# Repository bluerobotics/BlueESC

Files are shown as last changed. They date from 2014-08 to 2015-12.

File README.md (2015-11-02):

BlueESC
=======

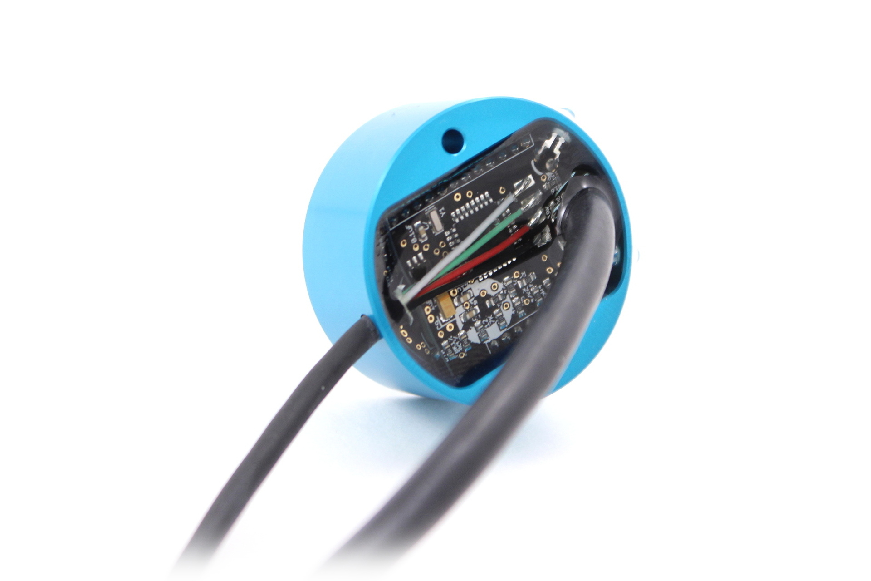
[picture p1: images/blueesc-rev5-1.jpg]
BlueESC Rev1 Prototype BlueESC Production Version


The BlueESC is a simple, open-source electronic speed controller for three-phase brushless motors. It is designed to run the [SimonK firmware](http://github.com/sim-/tgy) on an Atmega8 microcontroller.

The hardware is licensed under GPLv3. It was inspired by and draws from other open-source ESC projects including [AfroESC](https://code.google.com/p/afrodevices/), [WiiESC](https://code.google.com/p/wii-esc/), and others. We owe a big thanks to everyone who has shared their open-source ESC designs and firmware.

We also thank Bernhard Konze and SimonK for the [tgy firmware](http://github.com/sim-/tgy). Please see the firmware license at the top of [tgy.asm](https://github.com/bluerobotics/tgy/blob/master/tgy.asm). The firmware configuration files for the BlueESC are maintained in [our fork of the tgy project](http://github.com/bluerobotics/tgy).

##Features

* Atmega8 microcontroller
* PWM and I2C signal interfaces
* 5-22 volt input (2-5s lipo)
* Reprogrammable via PWM pin using bootloader (usblinker)
* Status and warning LED indicators
* Sensors for voltage, current, temperature, and RPM
* No battery-eliminator-circuit (BEC)
* N-Channel MOSFETs

##Current Generation: Rev. 5-8

The current major revision is designed to work with the [BlueRobotics T100 Thruster](http://www.bluerobotics.com/thruster/). It is highly compact and is potted in an aluminum enclosure that acts as a heat sink. The board is built with two 2-layer boards, one for the power electronics and one for logic. The boards are connected by headers. This allows components to be placed on three sides, simplifies design, and minimizes cost.

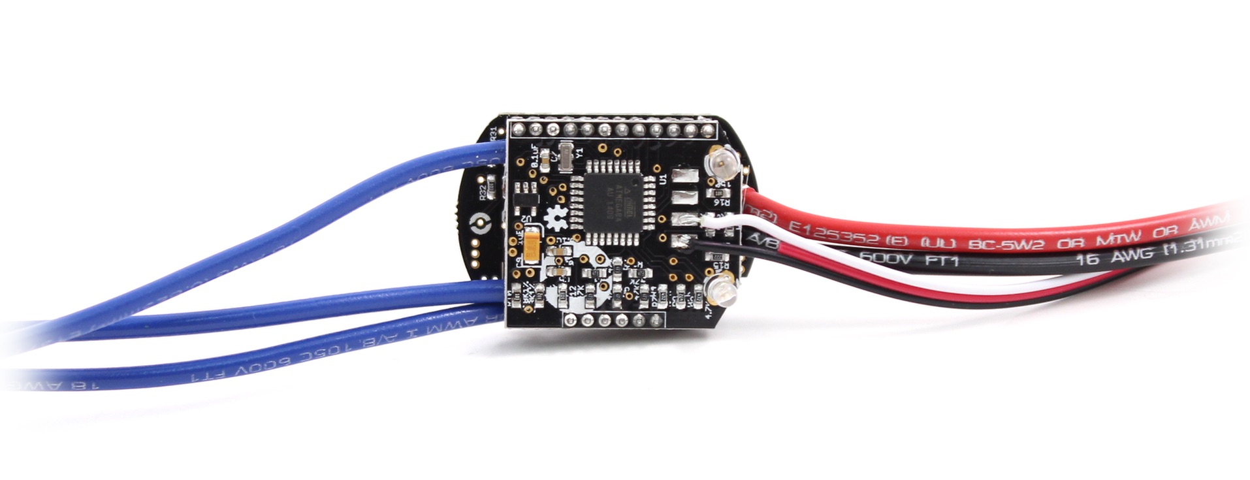
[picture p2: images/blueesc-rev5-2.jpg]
BlueESC Rev5 Board BlueESC Rev5 Without Enclosure


###Features

* Hall effect current sense IC (ACS711EX)
* Thermistor temperature sensor (10K)

###Specifications

* 6-22 volt input
* 25 amps continuous current (air)
* 35+ amps continuous current (water)
* 400 uF decoupling capacitance
* Enclosure diameter: 40 mm (1.58")
* Enclosure length: 18.5 mm (0.73")

###Design Files

**Schematic:** [BlueESC.pdf](https://github.com/bluerobotics/BlueESC/raw/master/BlueESC/BlueESC.pdf)

See repository for up-to-date EagleCAD schematic and board layout.

##Firmware Compilation

The BlueESC uses the [tgy firmware located in the BlueRobotics fork](https://github.com/bluerobotics/tgy).

*Mac:* (Uses Homebrew)

```bash
brew update
brew install avra
make blueesc.hex
```

##Initial Firmware Flashing

The BlueESC can be flashed using any AVR ISP programmer.

```bash
avrdude -c [programmer] -p m8 -U flash:w:blueesc.hex:i 
```

The fuses should be set per the instructions in the [tgy](http://github.com/sim-/tgy) instructions.

```bash
avrdude -c [programmer] -p m8 -U lfuse:w:0x3f:m -U hfuse:w:0xca:m
```

The Rev5 version of the board does not include an ISP header or pads. The microcontroller must be flashed with a special tool that connects directly to the microcontroller pins. Make sure that the board is powered when programming.

##Firmware Flashing Through Bootloader

Once the ESC has had the firmware (including bootloader) flashed the first time, it can be reprogrammed subsequently through the PWM input pin using a programmer like the [Turnigy USB Linker](http://www.hobbyking.com/hobbyking/store/__10628__turnigy_usb_linker_for_aquastar_super_brain.html). This can be done through the Makefile in the **tgy** project as follows.

```bash
make program_tgy_blueesc
```

It can also be done with avrdude and the compiled hex files as follows.

```bash
avrdude -c stk500v2 -b 19200 -P [programmer port] -p m8 -U flash:w:blueesc.hex:i
```

##I2C Commands and Address

*Please also see our [Arduino library for I2C ESC control](https://github.com/bluerobotics/Arduino_I2C_ESC).*

The I2C message format allows speed and direction to be set and voltage, current, rpm, temperature, and status to be requested.

###Speed Command (Register 0x00-0x01)
* cmd: Command, sent as int16_t. Full range, negative for reverse, positive for forward.
  * Forward: 0 to 32767
  * Reverse: 0 to -32767

####Bytes
* Byte 0: throttle_h
* Byte 1: throttle_l

###Sensor Data (Register 0x02-0x0A)
* pulse_count: Commutation pulses since last request. Sent as uint16_t.
  * Calculate rpm with pulse_count/dt*60/motor_pole_count
* voltage: ADC measurement scaled to 16 bits
  * Calculate voltage with voltage/2016
* temperature: ADC measurement scaled to 16 bits
  * Calculate temperature with the Steinhart equation
* current: ADC measurement scaled to 16 bits
  * Calculate current with (current-32767)/891

####Bytes
* Byte 0: pulse_count_h
* Byte 1: pulse_count_l
* Byte 2: voltage_h
* Byte 3: voltage_l
* Byte 4: temperature_h
* Byte 5: temperature_l
* Byte 6: current_h
* Byte 7: current_l
* Byte 8: 0xab (identifier to check if ESC is alive)

##Releases

v1.0 - Rev5. Currently shipping.

v1.1 - Rev6. Added PWM pull-down resistor and low pass filter for current sense. Switched to SMT LEDs. No changes to Power Board.

##Video

I2C Demonstration:

I2C Demonstration of BlueESC (https://www.youtube.com/watch?v=3BH41H-kpA8)

Testing of Final Prototype:

Final Prototype of BlueESC (https://www.youtube.com/watch?v=g5yOUzKvsxc)

Testing of First Prototype:

First Test of BlueESC (http://www.youtube.com/watch?feature=player_embedded&v=qJa0dBeoZHA)

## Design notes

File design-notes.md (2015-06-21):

##Design Notes for BlueESC

These design notes are written for the rev3 (two board) design, although they should pertain to the previous revisions as well.

##Component Selection

###MOSFETs

* Choose SiR158DP
* Max current is 30A and max duty cycle is about 33% (because it is three phase); Rdson is 0.0023 worst case and there are two FETs per phase so that P = 30^2*.33*.0023*2 = 1.36 W; This results in a junction-to-ambient rise of 23*1.36 = 31.3 C
* Output capacitance is 915 pF and input resistor is 100 ohm. Therefore, the RC time constant is 91.5 ns.
* According to (http://www.ti.com/lit/an/slva504/slva504.pdf), the switching power dissipation can be estimated as Psw = 0.5*(24V)*(30A)*(91.5E-9s)*(18000hz) = 0.60 W x 2 FETs = 1.20 W. This would lead to a temperature rise of 27.6 C.
* Using these numbers combined, the maximum temperature if ambient temp is 25C would be 84C. The max allowable temperature of the MOSFET is 150C.

#Other Collected Notes

MOSFETs:

Heat losses come from Rdson, which is usually small for most FETs. Rdson accounts for some of the heat.

More heat comes from the internal diodes, which are built into the silicon and are not Schottky. The reverse current spikes caused by the inductance of the motor causing back flowing current. The voltage drop turns into heat. This is most significant around the 50% duty cycle area. It's related to the switching frequency and the inductance of the motor.

If there is a lot of heat from diodes, external Schottky diodes could be added to reduce heat loss from voltage drop.

Choosing MOSFET and reading data sheet: The most important values for estimating performance are the temperature rise from junction to ambient per watt and the allowable temp, which should be derated. (Derates everything by x/0.6).

Most of the heat will be coming out of the big pad on the MOSFET, not the case. The copper there should be thick and large to distribute heat as well as possible. Hopefully the thermally conductive potting compound will help conduct heat from the traces.

The 100 ohm resistors that turn on the FETs are important to size properly, too large will turn them on slowly, increasing switching losses, and too small could cause the low side FETs to turn on accidentally. Recommended 22 ohm but  100 ohm was fine.

The charge pumps work by charging the capacitor to 12V when the low side is on, then when the high side turns on, the capacitor is already at 12V but the low side of the capacitor goes up to 12V, meaning that the high side of the capacitor is now 24V. It's only needed on the high side because the EMF of the motor is high when switching. Might be 10Vand Vin to MOSFET at 12V --> bad switching.

The charge pump diode needs to be sized the handle the current that rushes through it when switching. A small current limiting resistor could be used to help. 0.5-1.0 amp (what I have now) is more than sufficient.

The charge pump capacitor will never have more than the input voltage across it, so 12V or the max voltage.

If there are heat problems, it is most likely switching losses, then diode losses, then everything else.

CAPACITORS:

Recommend 500-1000uF for decoupling. Tantalums can be used, they have packages that are double high.

OTHER:

Strongly recommends current sensors to automatically limit current spikes when starting.

The software probably has a time delay between switching high and low, but you can also do it with hardware with a diode and sizing the resistors properly.

Guessed that motor inductance was 200-400 uH and that would be a low value for fast switching.

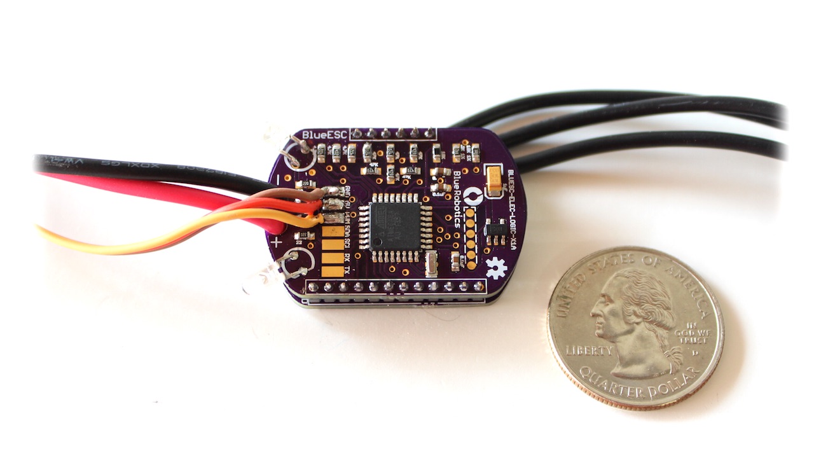
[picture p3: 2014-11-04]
images/blueesc-rev3-1.jpg

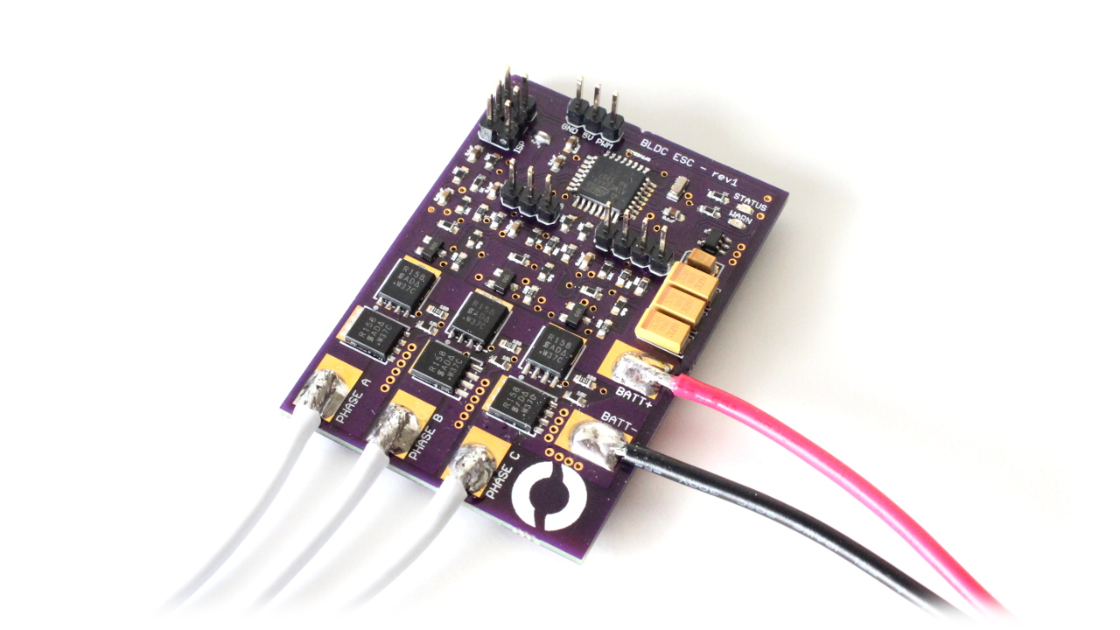
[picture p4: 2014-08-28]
images/blueesc-rev1-2.jpg

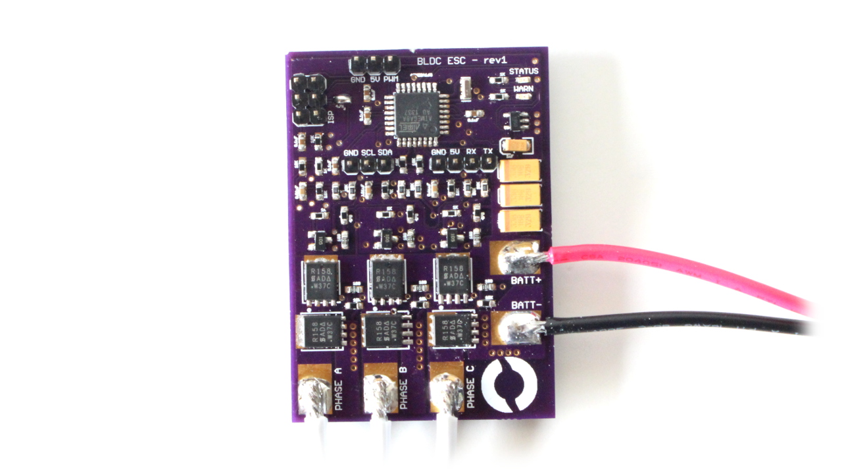
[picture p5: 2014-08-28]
images/blueesc-rev1-1.jpg

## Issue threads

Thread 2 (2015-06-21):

Low pass current sensor

rjehangir, 2015-06-21:
The current sensor bandwidth is too high causing slow measurements to require a large software low-pass filter for accuracy. A hardware low pass should be added to resolve this.

rjehangir, 2015-10-18:
A low pass filter has been added an makes a significant improvement to the current reading.

Closed 2015-10-18.

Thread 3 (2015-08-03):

PWM signal pull down

rjehangir, 2015-08-03:
Add a weak pull down to the PWM line so that it doesn't have to be grounded for I2C to work properly.

rjehangir, 2015-10-18:
A 470K resistor has been added and tested for correction function.

Closed 2015-10-18.

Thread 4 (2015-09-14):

BlueESC Control Logic I2C

gaitskell, 2015-09-14:
The manual doesn't explain what the red and blue LED's indicate on the integrated BlueESC. Also what does it mean when it beeps every few seconds?

I am able to read I2C data from the BlueESC but am unable to get prop spinning when writing I2C. Do you have any debug suggestions? Do you have to use PWM stop signal to activate motor, prior to being able to use I2C? I assume not? Do you have some I2C Python SBUS examples you could post to make sure I'm using your desired conventions? Thanks
Rickg@gaitskell.com

gaitskell, 2015-09-14:
Ok - so we figured it out by trial and error. I2C requires a write THROTTLE 0 for safety before a write THROTTLE 50 (finite speed). And you have to write <= 0.5 secs to avoid safety shutdown (which is a good feature). We filmed a video of the basic logic of operation and will post it on YouTube. Obviously, it would be great to get the online docs to include these aspects of I2C operation.

Closed 2015-09-14.

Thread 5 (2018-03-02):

Wrong RC time for the turn on of the upper FET in file "design-notes.md"

AGenchev, 2018-03-02:
Hello. I was looking for an ingenious design which would me allow to ditch the gate drivers I use, hence looked at the schematic in  https://github.com/bluerobotics/BlueESC/raw/master/BlueESC/BlueESC.pdf
But quickly realized that it will not perform on a par with the gate drivers (at least for the high side NMOSFETs).
The upper FETs are N-channel. They turn on with <b>positive</b> voltage on the gate relative to the source.
Watching the schematic in the https://github.com/bluerobotics/BlueESC/raw/master/BlueESC/BlueESC.pdf you can see that the upper FETs can get positive voltage on their gates from the high side of the capacitors via 100 Ω <b>plus 2.2 kΩ</b> resistors when the NPN transistors are OFF. This mean that the total resistance on this path is 2.3 kΩ, so the turn on RC constant is 10-20 times longer. E.t. instead of 100 nS, it goes at least to 1000 nS. This should lead to more heat generated by the upper FETs (if the charging pumps work as intended and supply higher than Vcc voltage to turn on the upper FETs).  You should use either more sophisticated push-pull high side gate driver or use an IC gate driver (which of course will make the BOM with higher cost).

Williangalvani, 2019-04-01:
As this repository is being archived and will see no further development, all issues are being closed.

Closed 2019-04-01.

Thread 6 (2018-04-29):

modular ESC

mkeyno, 2018-04-29:
Hi, sorry to open ticket for my question , actually I intend to made modular ESC in way that controller + gate driver is separated from Mosfets pcb , hence I could increase module ampere by adding parallel Mosfet in the Mosfets pcb, I really appreciated to have your advise or if you know open HW/SW sources let me know

Williangalvani, 2019-04-01:
As this repository is being archived and will see no further development, all issues are being closed.

Closed 2019-04-01.

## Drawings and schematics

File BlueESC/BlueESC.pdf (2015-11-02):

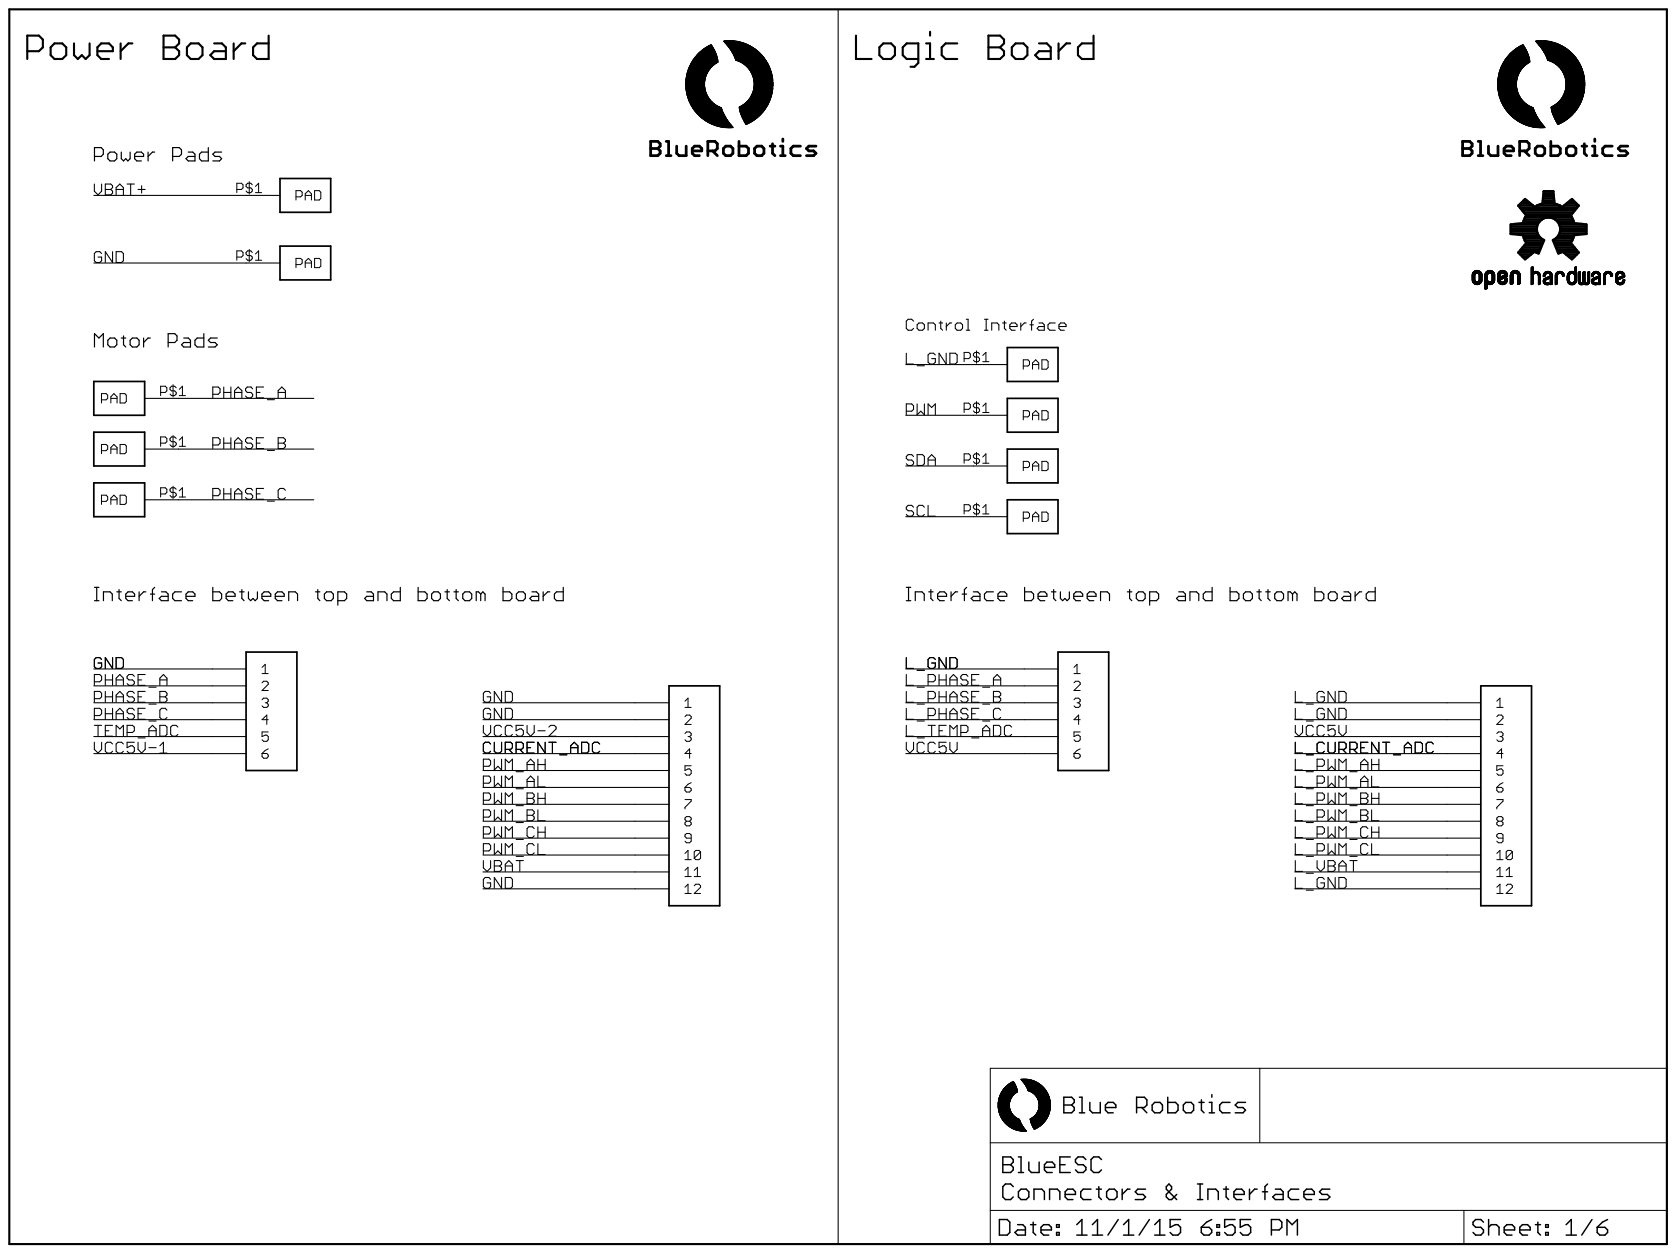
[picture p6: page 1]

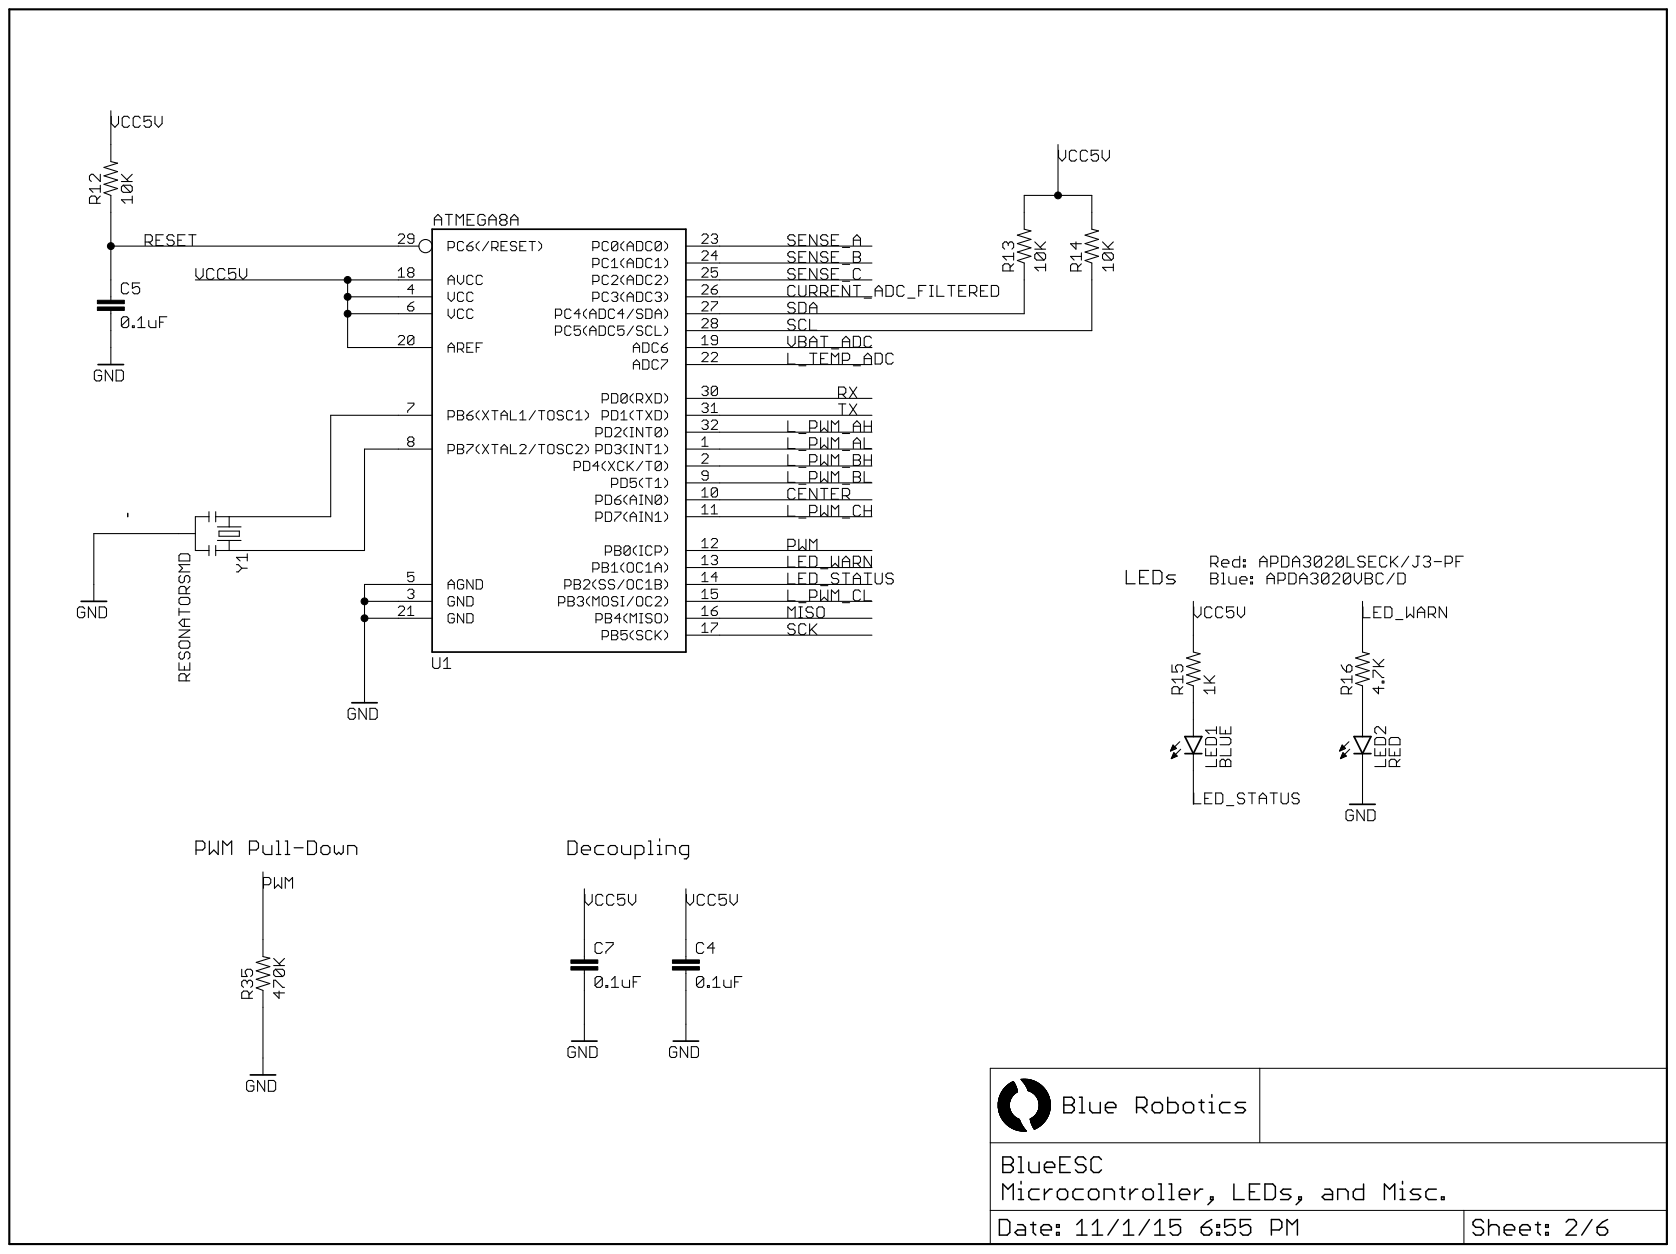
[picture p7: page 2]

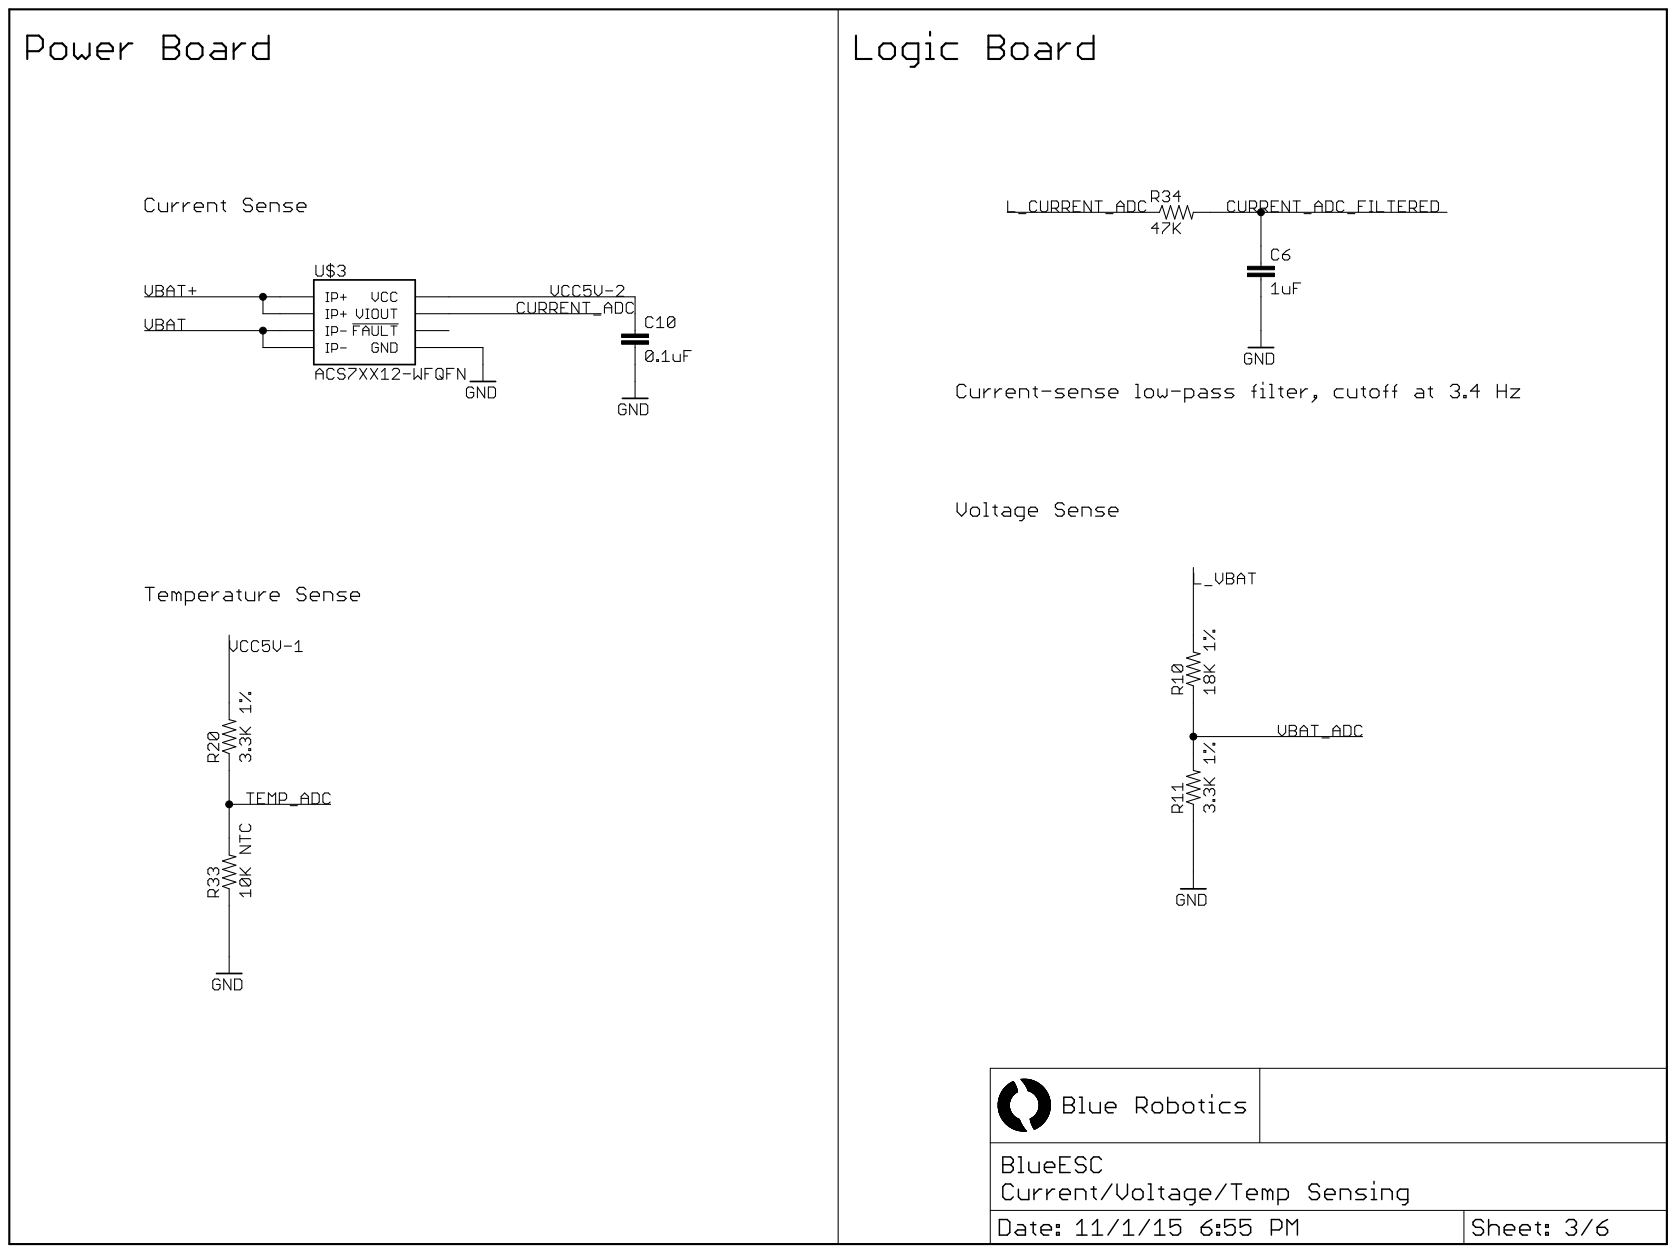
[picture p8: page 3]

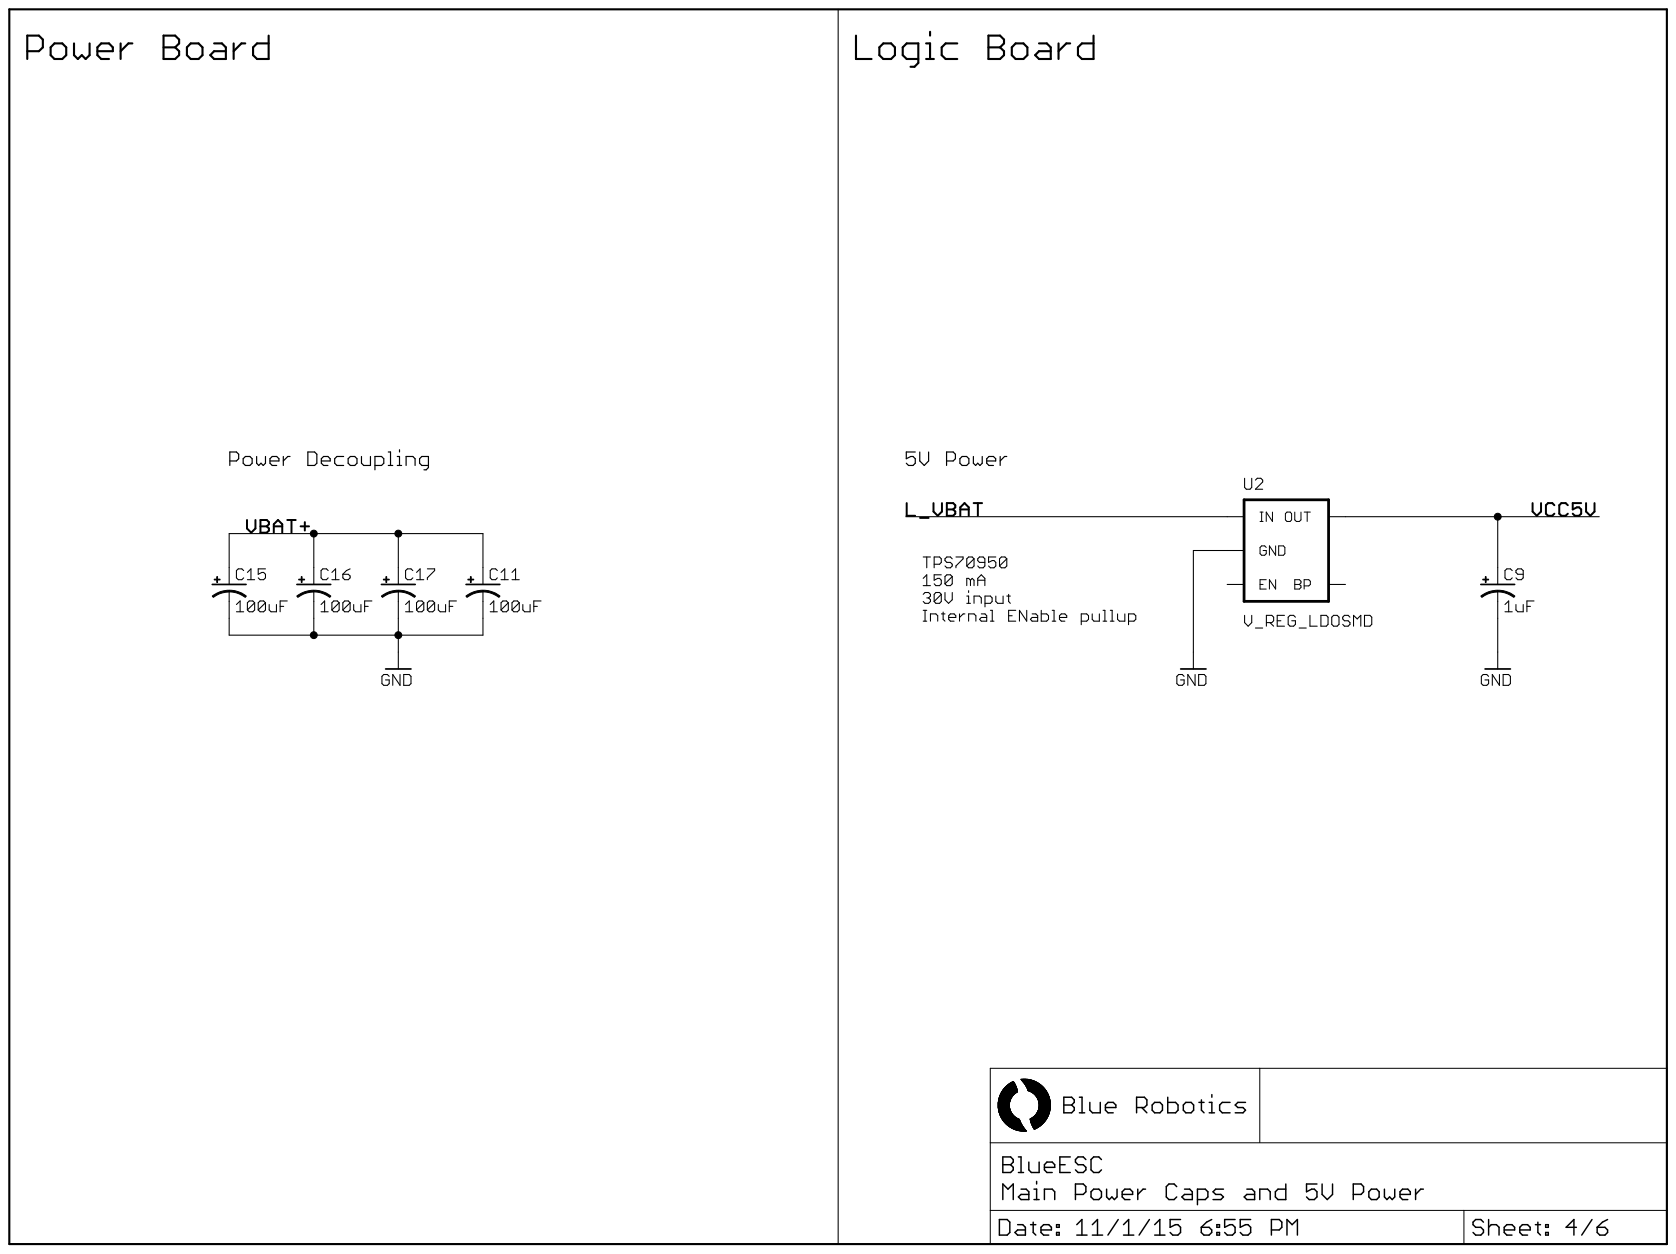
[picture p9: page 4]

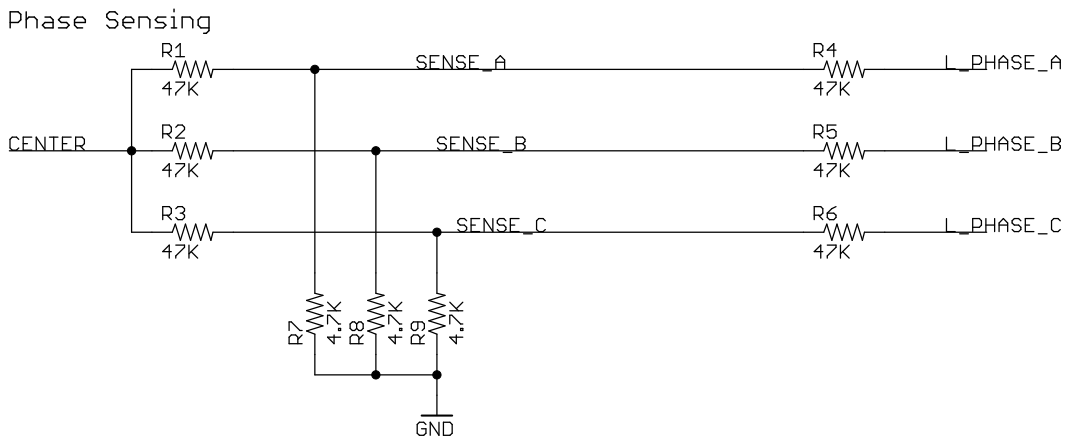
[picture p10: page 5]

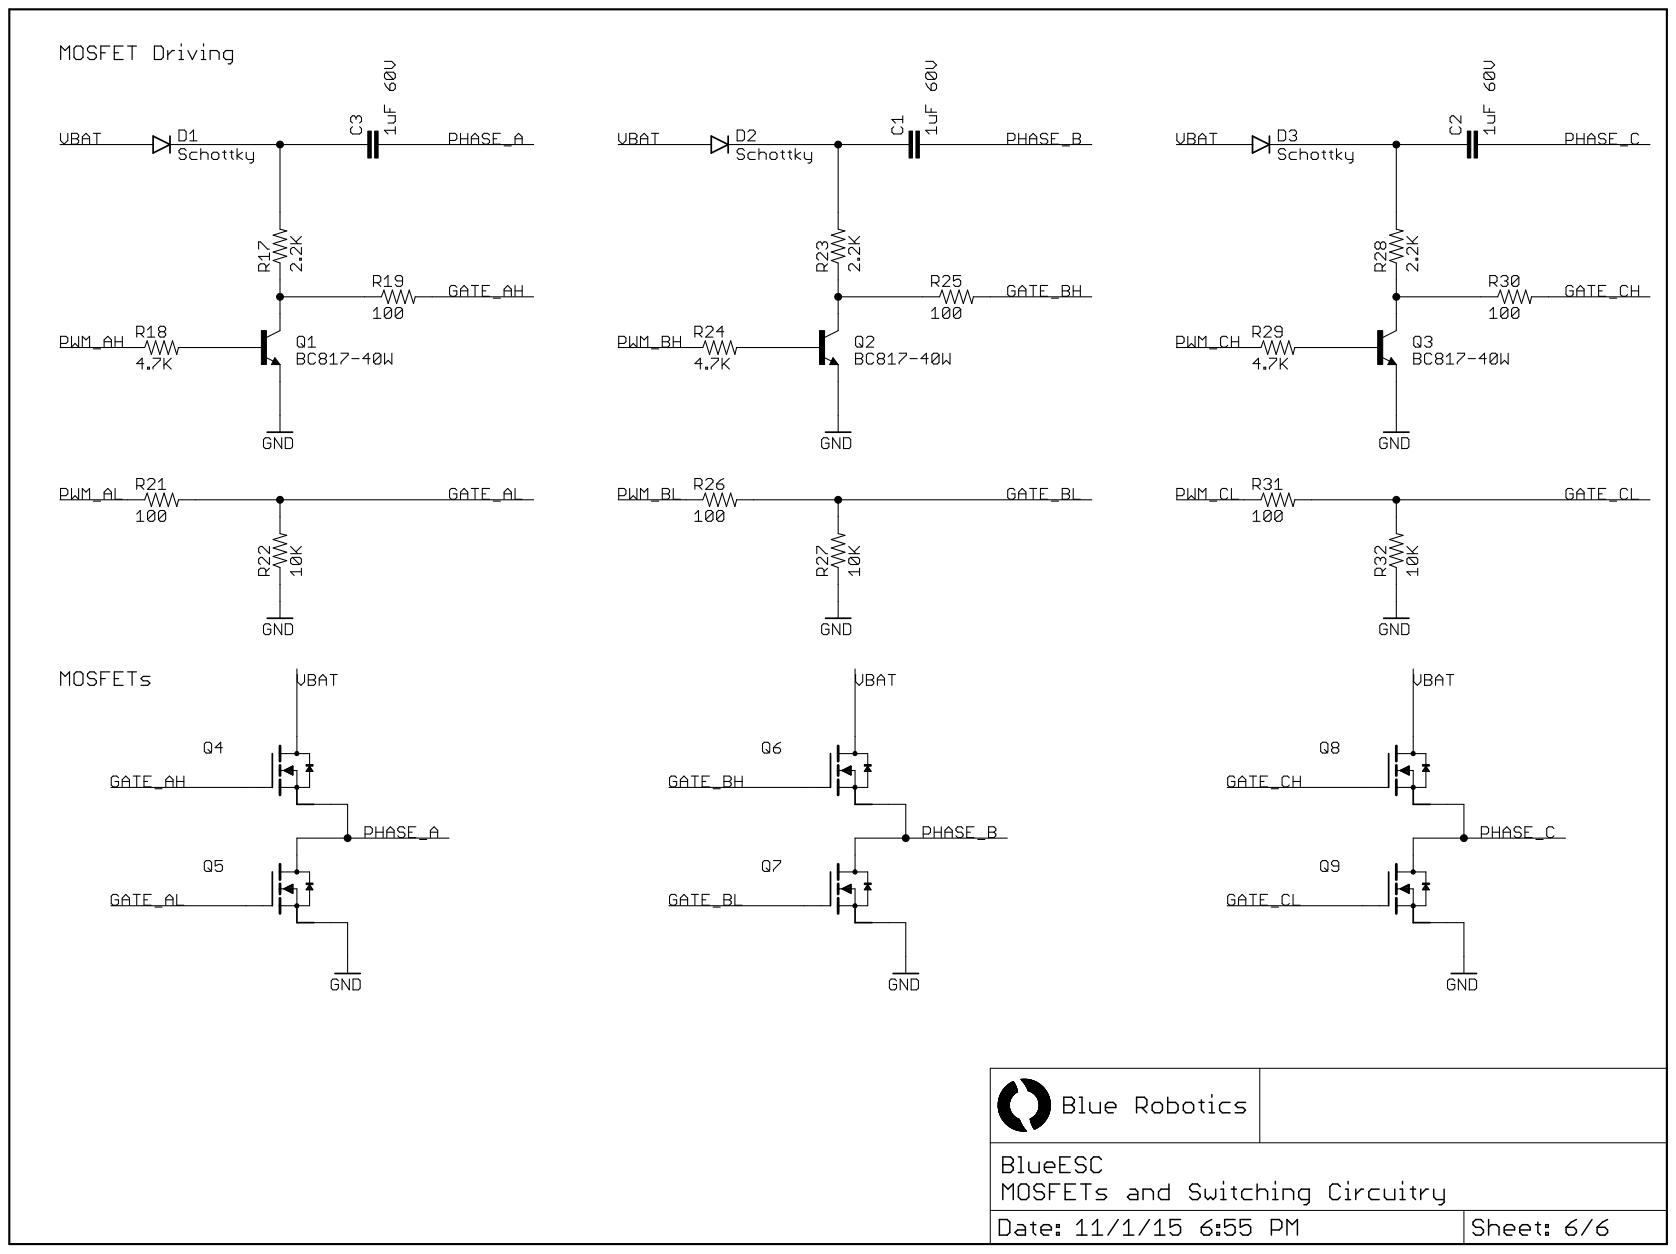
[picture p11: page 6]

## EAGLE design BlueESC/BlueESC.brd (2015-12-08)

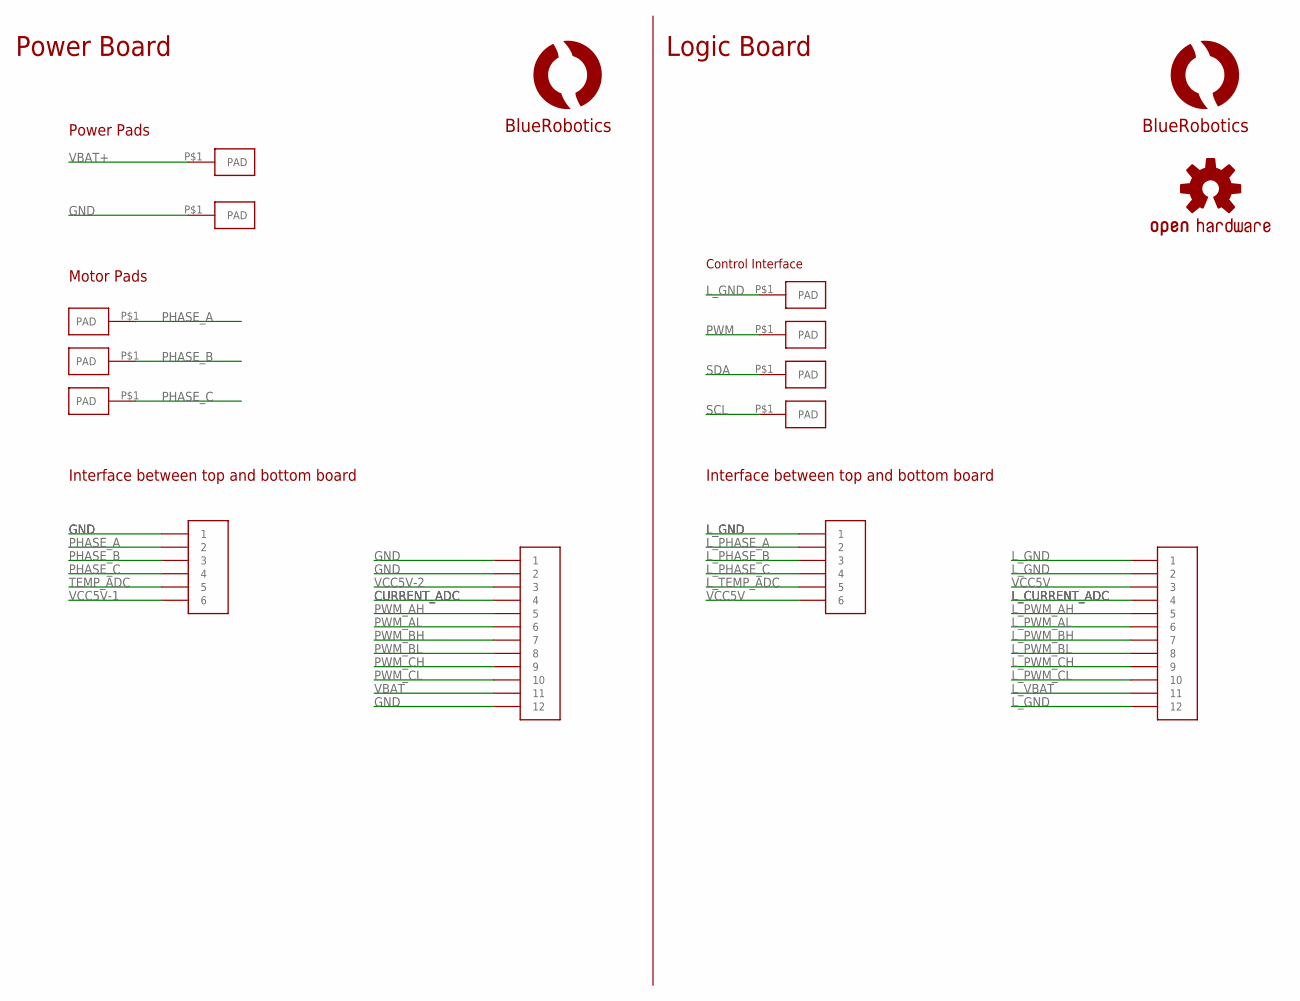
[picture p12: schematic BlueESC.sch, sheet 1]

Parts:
LOGO1: OSHW-LOGOS; OSHW-LOGO-S
U$1, U$2: PADPTH-MED; PAD-PTH-MED-1
U$4, U$16: HEADER-62MM; HEADER-2MM-6POS
U$5, U$6, U$7: PAD18AWG; PAD-PTH-18AWG-1
U$8, U$17: HEADER-122MM; HEADER-2MM-12POS
U$9: LOGOBR-LOGO-S; BR-LOGO-SMALL
U$10: LOGOBR-LOGO-M; BR-LOGO-MEDIUM
U$11, U$12, U$13, U$14: PAD1.5X3MM; PAD-1.5X3MM

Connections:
CURRENT_ADC: U$8.P$4 (4); also elsewhere on the board
GND: U$2.P$1, U$4.P$1 (1), U$8.P$1 (1), U$8.P$2 (2), U$8.P$12 (12); also elsewhere on the board
L_CURRENT_ADC: U$17.P$4 (4); also elsewhere on the board
L_GND: U$11.P$1, U$16.P$1 (1), U$17.P$1 (1), U$17.P$2 (2), U$17.P$12 (12); also elsewhere on the board
L_PHASE_A: U$16.P$2 (2); also elsewhere on the board
L_PHASE_B: U$16.P$3 (3); also elsewhere on the board
L_PHASE_C: U$16.P$4 (4); also elsewhere on the board
L_PWM_AH: U$17.P$5 (5); also elsewhere on the board
L_PWM_AL: U$17.P$6 (6); also elsewhere on the board
L_PWM_BH: U$17.P$7 (7); also elsewhere on the board
L_PWM_BL: U$17.P$8 (8); also elsewhere on the board
L_PWM_CH: U$17.P$9 (9); also elsewhere on the board
L_PWM_CL: U$17.P$10 (10); also elsewhere on the board
L_TEMP_ADC: U$16.P$5 (5); also elsewhere on the board
L_VBAT: U$17.P$11 (11); also elsewhere on the board
PHASE_A: U$4.P$2 (2), U$5.P$1; also elsewhere on the board
PHASE_B: U$4.P$3 (3), U$6.P$1; also elsewhere on the board
PHASE_C: U$4.P$4 (4), U$7.P$1; also elsewhere on the board
PWM: U$14.P$1; also elsewhere on the board
PWM_AH: U$8.P$5 (5); also elsewhere on the board
PWM_AL: U$8.P$6 (6); also elsewhere on the board
PWM_BH: U$8.P$7 (7); also elsewhere on the board
PWM_BL: U$8.P$8 (8); also elsewhere on the board
PWM_CH: U$8.P$9 (9); also elsewhere on the board
PWM_CL: U$8.P$10 (10); also elsewhere on the board
SCL: U$13.P$1; also elsewhere on the board
SDA: U$12.P$1; also elsewhere on the board
TEMP_ADC: U$4.P$5 (5); also elsewhere on the board
VBAT: U$8.P$11 (11); also elsewhere on the board
VBAT+: U$1.P$1; also elsewhere on the board
VCC5V: U$16.P$6 (6), U$17.P$3 (3); also elsewhere on the board
VCC5V-1: U$4.P$6 (6); also elsewhere on the board
VCC5V-2: U$8.P$3 (3); also elsewhere on the board

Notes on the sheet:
Power Pads
Motor Pads
Interface between top and bottom board
Control Interface
Power Board
Logic Board

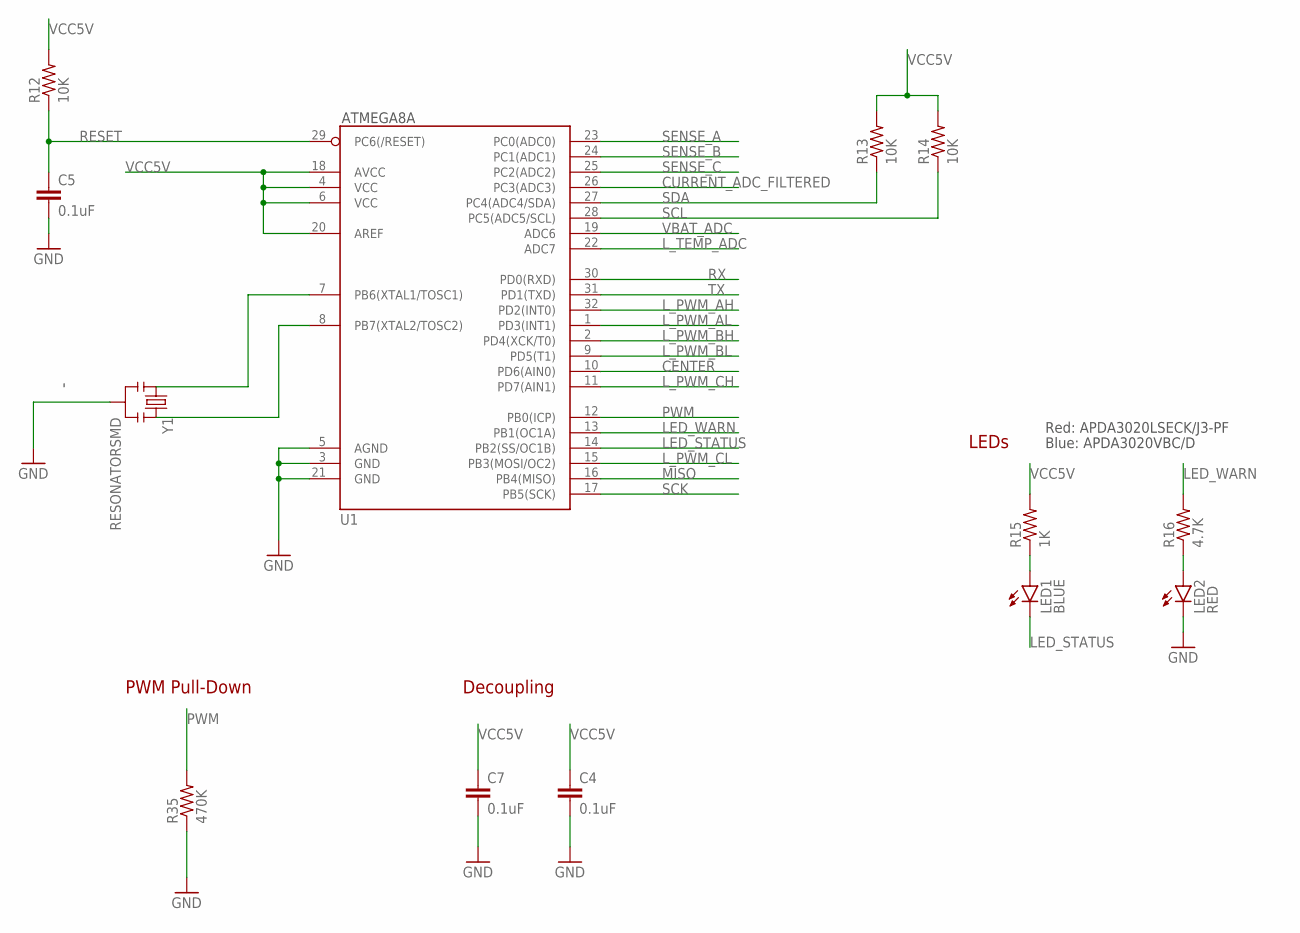
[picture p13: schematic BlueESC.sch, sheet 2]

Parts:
C4, C5, C7: 0.1uF; 0603-CAP
LED1: BLUE; SMT-LED-3X2-RA
LED2: RED; SMT-LED-3X2-RA
R12, R13, R14: 10K; 0603-RES
R15: 1K; 0603-RES
R16: 4.7K; 0603-RES
R35: 470K; 0603-RES
U1: ATMEGA168; TQFP32-08
Y1: RESONATORSMD; RESONATOR-SMD

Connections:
CENTER: U1.10 (PD6(AIN0)); also elsewhere on the board
CURRENT_ADC_FILTERED: U1.26 (PC3(ADC3)); also elsewhere on the board
LED_STATUS: LED1.2 (C), U1.14 (PB2(SS/OC1B))
LED_WARN: R16.2, U1.13 (PB1(OC1A))
L_GND: C4.2, C5.2, C7.2, LED2.2 (C), R35.1, U1.3 (GND), U1.5 (AGND), U1.21 (GND), Y1.2; also elsewhere on the board
L_PWM_AH: U1.32 (PD2(INT0)); also elsewhere on the board
L_PWM_AL: U1.1 (PD3(INT1)); also elsewhere on the board
L_PWM_BH: U1.2 (PD4(XCK/T0)); also elsewhere on the board
L_PWM_BL: U1.9 (PD5(T1)); also elsewhere on the board
L_PWM_CH: U1.11 (PD7(AIN1)); also elsewhere on the board
L_PWM_CL: U1.15 (PB3(MOSI/OC2)); also elsewhere on the board
L_TEMP_ADC: U1.22 (ADC7); also elsewhere on the board
MISO: U1.16 (PB4(MISO))
unnamed: LED2.1 (A), R16.1
unnamed: U1.7 (PB6(XTAL1/TOSC1)), Y1.1
unnamed: U1.8 (PB7(XTAL2/TOSC2)), Y1.3
unnamed: LED1.1 (A), R15.1
PWM: R35.2, U1.12 (PB0(ICP)); also elsewhere on the board
RESET: C5.1, R12.1, U1.29 (PC6(/RESET))
RX: U1.30 (PD0(RXD))
SCK: U1.17 (PB5(SCK))
SCL: R14.1, U1.28 (PC5(ADC5/SCL)); also elsewhere on the board
SDA: R13.1, U1.27 (PC4(ADC4/SDA)); also elsewhere on the board
SENSE_A: U1.23 (PC0(ADC0)); also elsewhere on the board
SENSE_B: U1.24 (PC1(ADC1)); also elsewhere on the board
SENSE_C: U1.25 (PC2(ADC2)); also elsewhere on the board
TX: U1.31 (PD1(TXD))
VBAT_ADC: U1.19 (ADC6); also elsewhere on the board
VCC5V: C4.1, C7.1, R12.2, R13.2, R14.2, R15.2, U1.4 (VCC), U1.6 (VCC), U1.18 (AVCC), U1.20 (AREF); also elsewhere on the board

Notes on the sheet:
ATMEGA8A
Decoupling
LEDs
Red: APDA3020LSECK/J3-PF
Blue: APDA3020VBC/D
PWM Pull-Down

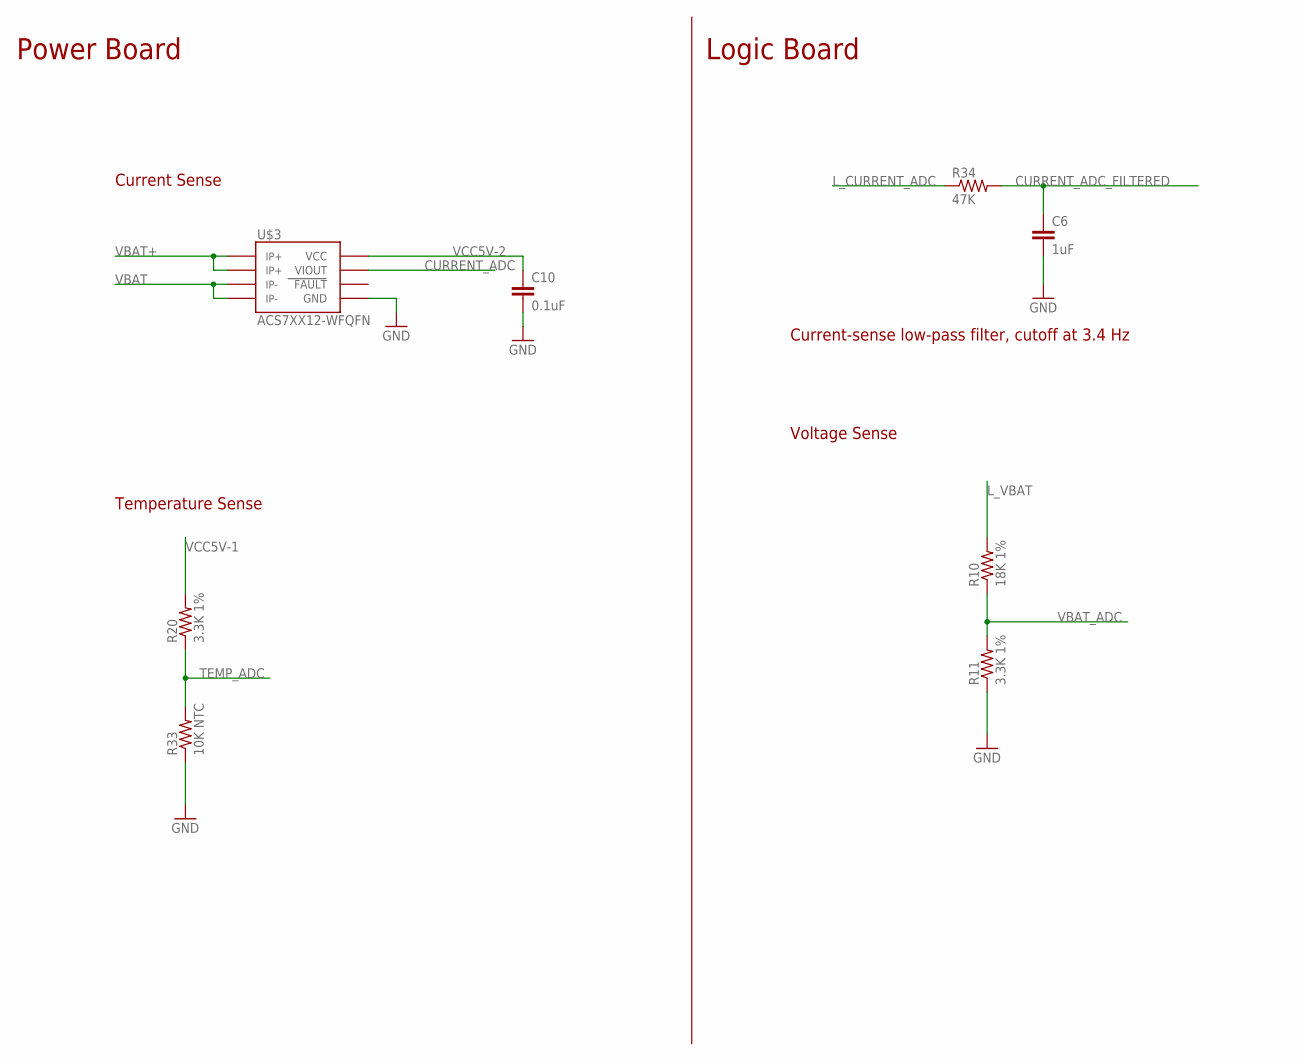
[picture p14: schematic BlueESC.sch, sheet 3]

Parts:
C6: 1uF; 0603-CAP
C10: 0.1uF; 0603-CAP
R10: 18K 1%; 0603-RES
R11, R20: 3.3K 1%; 0603-RES
R33: 10K NTC; 0603-RES
R34: 47K; 0603-RES
U$3: ACS7XX12-WFQFN; 12-WFQFN

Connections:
CURRENT_ADC: U$3.VIOUT; also elsewhere on the board
CURRENT_ADC_FILTERED: C6.1, R34.2; also elsewhere on the board
GND: C10.2, R33.1, U$3.GND; also elsewhere on the board
L_CURRENT_ADC: R34.1; also elsewhere on the board
L_GND: C6.2, R11.1; also elsewhere on the board
L_VBAT: R10.2; also elsewhere on the board
TEMP_ADC: R20.1, R33.2; also elsewhere on the board
VBAT: U$3.IP-1, U$3.IP-2; also elsewhere on the board
VBAT+: U$3.IP+1, U$3.IP+2; also elsewhere on the board
VBAT_ADC: R10.1, R11.2; also elsewhere on the board
VCC5V-1: R20.2; also elsewhere on the board
VCC5V-2: C10.1, U$3.VCC; also elsewhere on the board

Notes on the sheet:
Power Board
Logic Board
Current-sense low-pass filter, cutoff at 3.4 Hz
Voltage Sense
Current Sense
Temperature Sense

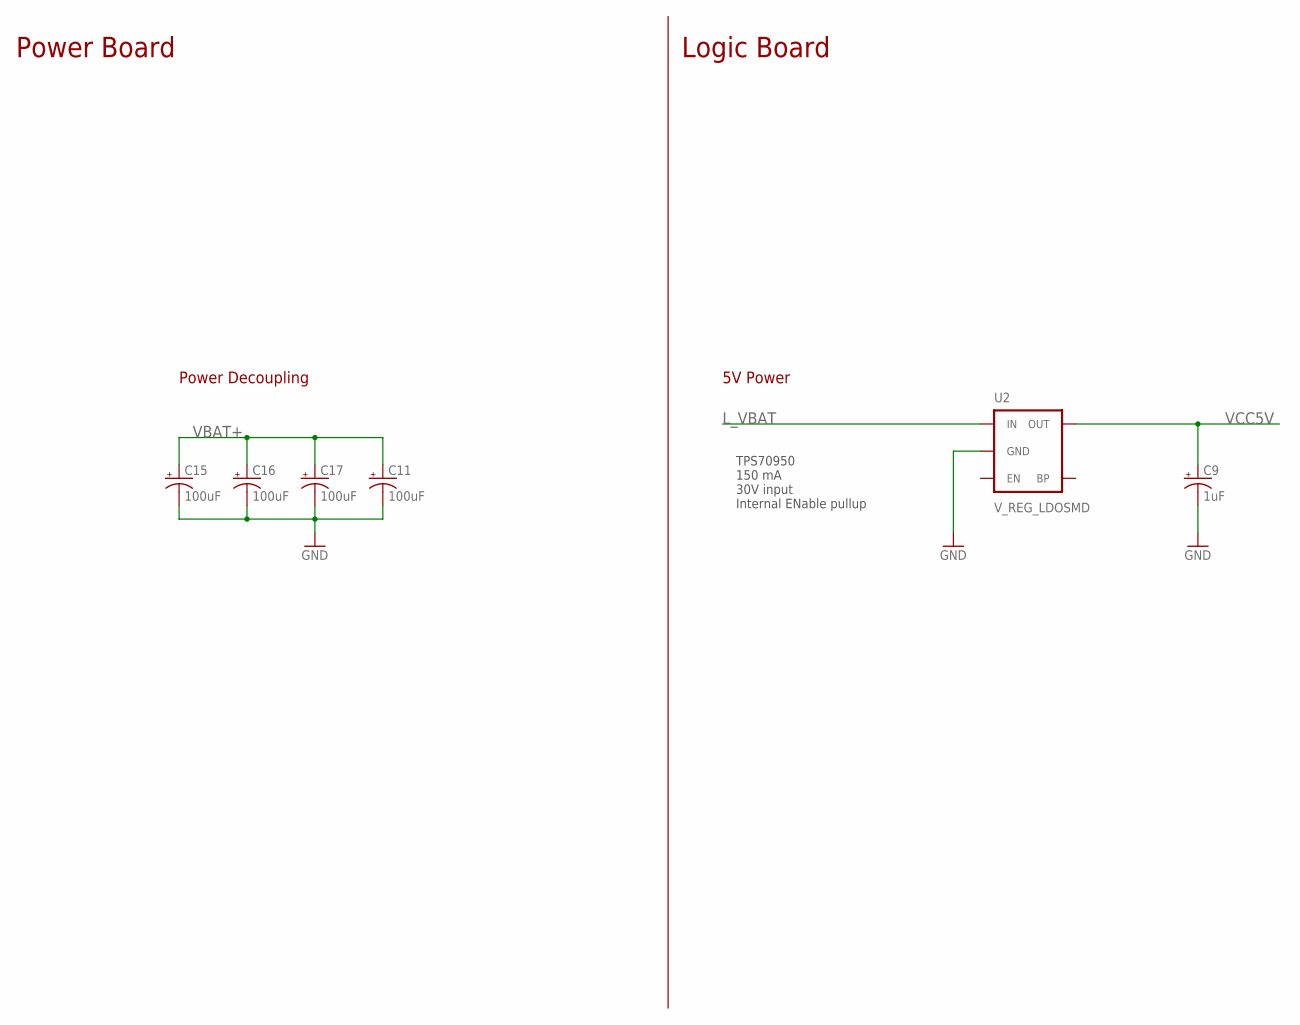
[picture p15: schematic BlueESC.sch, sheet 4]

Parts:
C9: 1uF; EIA3216
C11, C15, C16, C17: 100uF; EIA7343
U2: V_REG_LDOSMD; SOT23-5

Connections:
GND: C11.C (-), C15.C (-), C16.C (-), C17.C (-); also elsewhere on the board
L_GND: C9.C (-), U2.2 (GND); also elsewhere on the board
L_VBAT: U2.1 (IN); also elsewhere on the board
VBAT+: C11.A (+), C15.A (+), C16.A (+), C17.A (+); also elsewhere on the board
VCC5V: C9.A (+), U2.5 (OUT); also elsewhere on the board

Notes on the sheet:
Power Board
Logic Board
Power Decoupling
5V Power
TPS70950 150 mA 30V input Internal ENable pullup

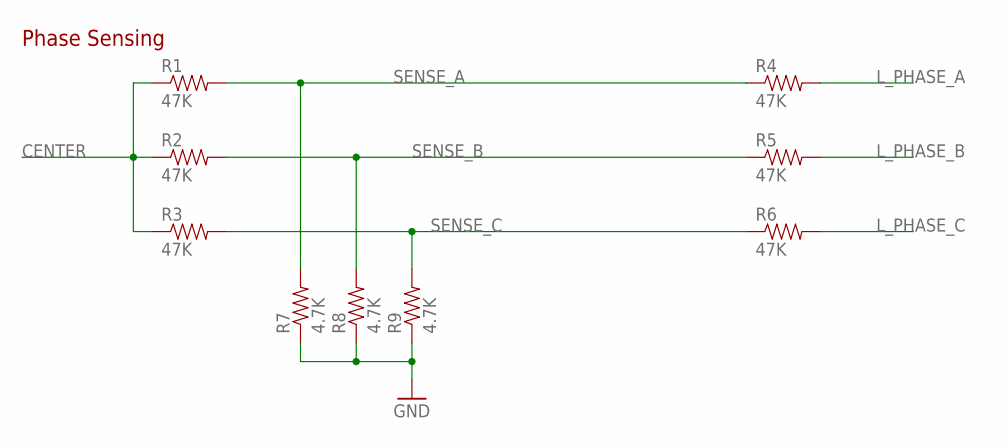
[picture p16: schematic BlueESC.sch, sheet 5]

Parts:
R1, R2, R3, R4, R5, R6: 47K; 0603-RES
R7, R8, R9: 4.7K; 0603-RES

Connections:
CENTER: R1.1, R2.1, R3.1; also elsewhere on the board
L_GND: R7.1, R8.1, R9.1; also elsewhere on the board
L_PHASE_A: R4.2; also elsewhere on the board
L_PHASE_B: R5.2; also elsewhere on the board
L_PHASE_C: R6.2; also elsewhere on the board
SENSE_A: R1.2, R4.1, R7.2; also elsewhere on the board
SENSE_B: R2.2, R5.1, R8.2; also elsewhere on the board
SENSE_C: R3.2, R6.1, R9.2; also elsewhere on the board

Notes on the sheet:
Phase Sensing

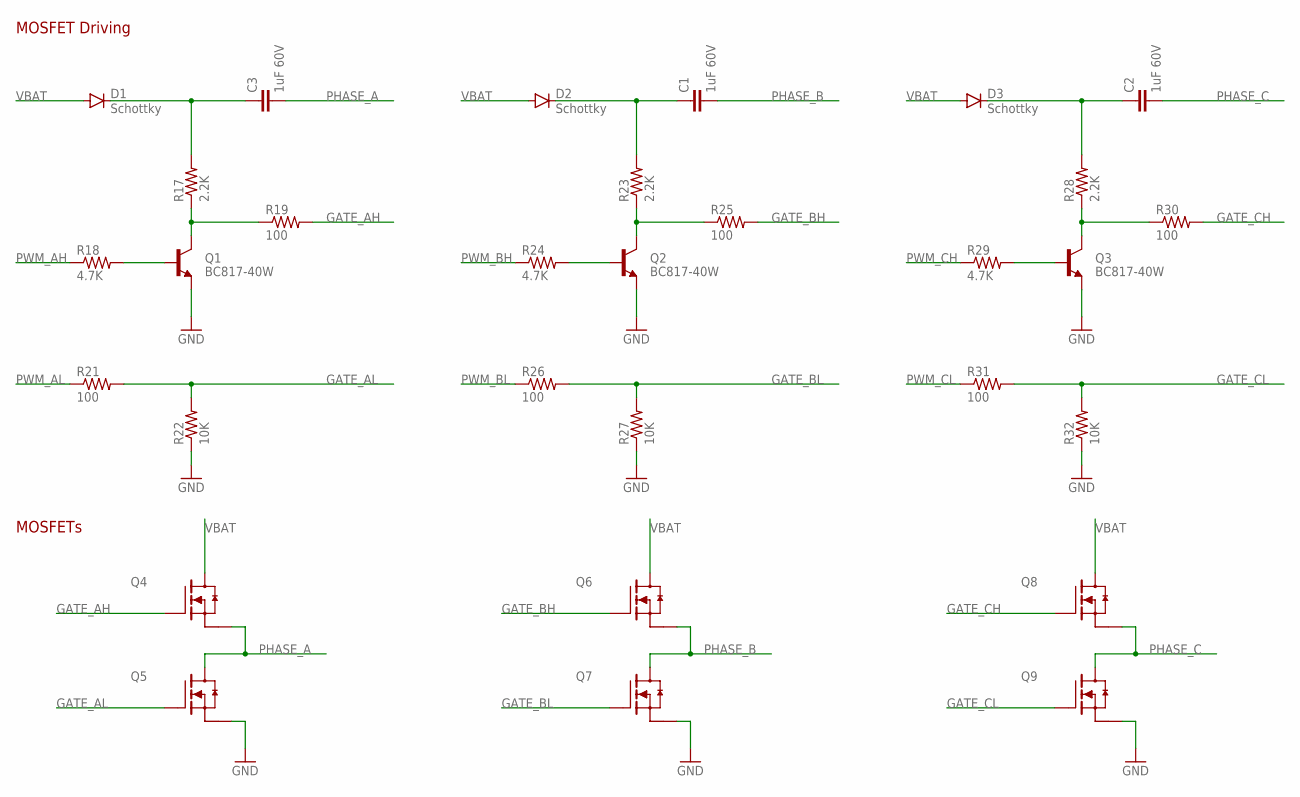
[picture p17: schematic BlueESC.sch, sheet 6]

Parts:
C1, C2, C3: 1uF 60V; 0805
D1, D2, D3: Schottky; SOD-323
Q1, Q2, Q3: BC817-40W; SOT23
Q4, Q5, Q6, Q7, Q8, Q9: MOSFET-NCHANNEL; TDSON-8
R17, R23, R28: 2.2K; 0603-RES
R18, R24, R29: 4.7K; 0603-RES
R19, R21, R25, R26, R30, R31: 100; 0603-RES
R22, R27, R32: 10K; 0603-RES

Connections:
GATE_AH: Q4.G, R19.2
GATE_AL: Q5.G, R21.2, R22.2
GATE_BH: Q6.G, R25.2
GATE_BL: Q7.G, R26.2, R27.2
GATE_CH: Q8.G, R30.2
GATE_CL: Q9.G, R31.2, R32.2
GND: Q1.2 (E), Q2.2 (E), Q3.2 (E), Q5.S1 (S), Q5.S2 (S), Q5.S3 (S), Q7.S1 (S), Q7.S2 (S), Q7.S3 (S), Q9.S1 (S), Q9.S2 (S), Q9.S3 (S), R22.1, R27.1, R32.1; also elsewhere on the board
unnamed: Q1.1 (B), R18.2
unnamed: Q1.3 (C), R17.1, R19.1
unnamed: Q2.1 (B), R24.2
unnamed: Q2.3 (C), R23.1, R25.1
unnamed: Q3.1 (B), R29.2
unnamed: Q3.3 (C), R28.1, R30.1
unnamed: C3.1, D1.C, R17.2
unnamed: C1.1, D2.C, R23.2
unnamed: C2.1, D3.C, R28.2
PHASE_A: C3.2, Q4.S1 (S), Q4.S2 (S), Q4.S3 (S), Q5.D; also elsewhere on the board
PHASE_B: C1.2, Q6.S1 (S), Q6.S2 (S), Q6.S3 (S), Q7.D; also elsewhere on the board
PHASE_C: C2.2, Q8.S1 (S), Q8.S2 (S), Q8.S3 (S), Q9.D; also elsewhere on the board
PWM_AH: R18.1; also elsewhere on the board
PWM_AL: R21.1; also elsewhere on the board
PWM_BH: R24.1; also elsewhere on the board
PWM_BL: R26.1; also elsewhere on the board
PWM_CH: R29.1; also elsewhere on the board
PWM_CL: R31.1; also elsewhere on the board
VBAT: D1.A, D2.A, D3.A, Q4.D, Q6.D, Q8.D; also elsewhere on the board

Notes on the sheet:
MOSFETs
MOSFET Driving

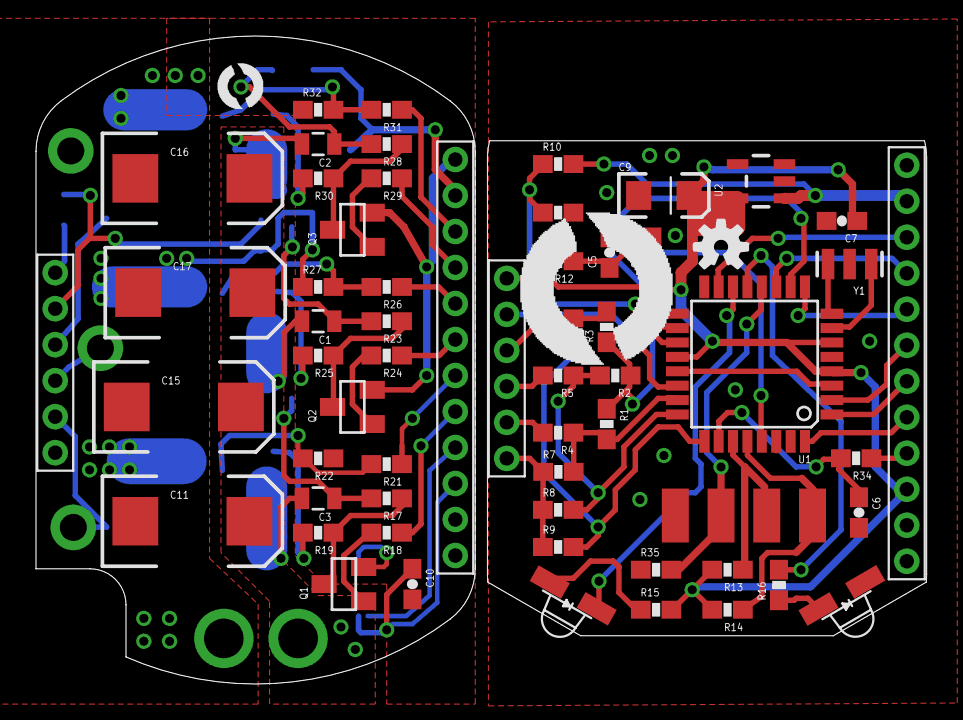
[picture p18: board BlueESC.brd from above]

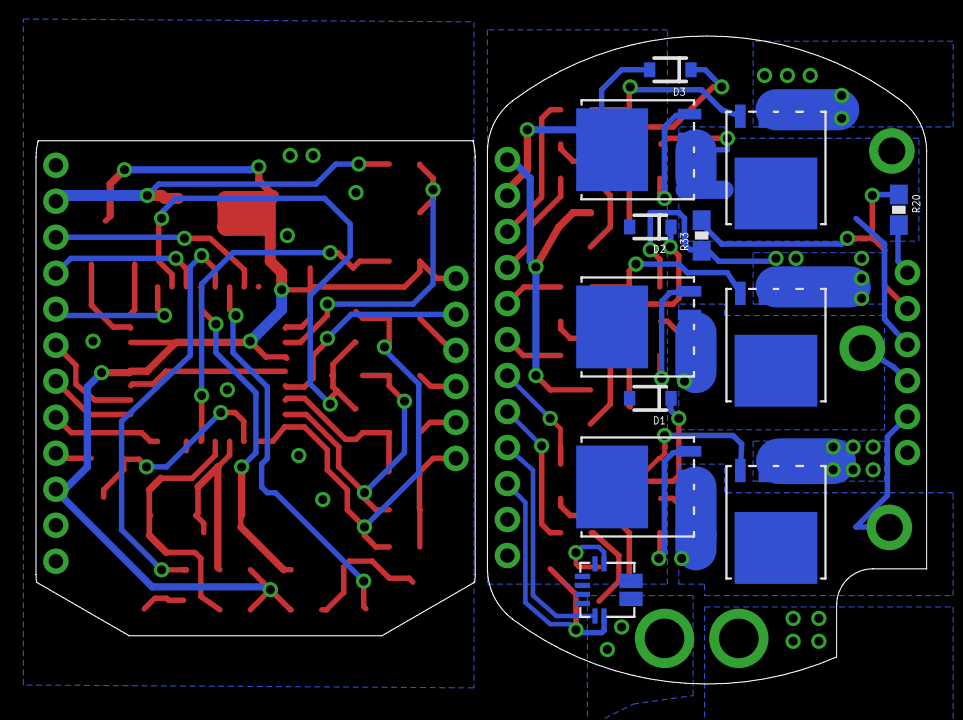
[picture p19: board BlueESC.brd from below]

Board: 2 copper layers, 49.5 x 36.0 mm, 82 parts (15 on the bottom side), 61 nets.

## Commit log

2014-08-26 Initial commit of rev1 schematic and board layout. They have been successfully tested.
    [BlueESC.brd, BlueESC.sch]
2014-08-26 Update README.md
    Add mosfet type to readme.
2014-08-27 Removed misleading label from MOSFETS on board layout.
    [BlueESC.brd, BlueESC.sch]
2014-08-27 Update README.md
    Updated current ratings.
2014-08-28 Added photos of the BlueESC rev 1 prototype.
2014-08-30 Added diodes and capacitors near fets. Need to verify necessary package sizes.
    [BlueESC.brd, BlueESC.sch]
2014-09-02 Small changes.
    [BlueESC.brd, BlueESC.sch]
2014-09-03 Changed value of charge pump capacitors because there are more package sizes available for 1.0uF.
    [BlueESC.brd, BlueESC.sch]
2014-09-03 Removed sense filtering capacitors and changed voltage divider resistor values.
    [BlueESC.brd, BlueESC.sch]
2014-09-03 Updated schematic to reflect changes made to rev1a prototype. This includes different passive values and the addition of charge pumps for the n-channel fets.
    [BlueESC.brd, BlueESC.sch]
2014-09-03 Placed more components on board layout.
    [BlueESC.brd, BlueESC.sch]
2014-09-19 Small changes before testing of rev1a.
    [BlueESC.brd]
2014-09-22 Added ACS71X to the schematic and board layout to measure current.
    [BlueESC.brd, BlueESC.sch]
2014-09-30 Updated rev3 schematic and split the schematic into two boards.
    [BlueESC.brd, Logic.brd, Logic.sch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]
2014-10-01 Rev3 (two boards) laid out and ready to go. Final review may create a few changes.
    [ISP-Adapter.brd, ISP-Adapter.sch, Logic.brd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]
2014-10-07 Rev 3 changes. Boards have been ordered.
    [Logic.brd, Logic.sch, Power.brd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]
2014-10-19 Removed rev 2 files. This version was a 4-layer board that was never completed.
    [BlueESC.brd, BlueESC.sch]
2014-11-04 I2C updates to readme.
2014-11-04 Added revision 4 files. No major changes yet except for decoupling capacitor values.
    [Logic.brd, Logic.sch, Power.brd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]
2014-12-11 Enlarged wire holes for 16AWG.
    [Power.brd, Power.sch]
2014-12-26 Commit before major changes to rev 4
    [Logic.brd, Logic.sch]
2015-01-08 Major updates on revision 4 include rearranged components, removal of programming pins, and new board shapes.
    [Logic.brd, Logic.sch, Power.brd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]
2015-02-16 Minor changes before ordering production boards.
    [Logic.brd, Logic.sch, Power.brd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]
2015-05-29 Updated I2C protocol to the actual protocol that will be used.
2015-05-29 Updated the speed command I2C.
2015-06-21 Added rev 5 board and schematic files.
    [Logic.brd, Logic.sch, Power.brd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]
2015-06-21 Removed old revisions.
    [BlueESC.brd, BlueESC.sch, ISP-Adapter.brd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]
2015-06-21 Moved current revision to a new folder.
    [Logic.brd, Logic.sch, Power.brd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]
2015-06-21 Added link to Arduino library.
2015-08-12 Switch to SMT LEDs.
    [Logic.brd, Logic.sch]
2015-08-12 Added PWM pull-down resistor.
    [Logic.brd, Logic.sch]
2015-08-16 New logic board prototype ordered 8/14/15.
    [Logic.brd, Logic.sch]
2015-09-24 Updated PWM pull down to 470K to avoid avoid beating out the internal pull-ups used in ArduinoUSBLinker.
    [Logic.brd, Logic.sch]
2015-11-02 Combined logic and power boards into a single board. This is done for several reasons. The first is to create a consistent single schematic to help others view the design. The second is for manufactu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
    [BlueESC.brd, BlueESC.sch, Logic.brd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]
2015-11-02 Reorganized combined schematic and broke everything into multiple sheets for easier viewing.
    [BlueESC.brd, BlueESC.sch]
2015-11-02 Put R20 on back of power board to minimize soldering errors.
    [BlueESC.brd]
2015-11-02 Updated MOSFET footprint to TDSON-8 to accommodate new FET and to fix potential soldering errors. This should still fit the SiR158DP as well.
    [BlueESC.brd, BlueESC.sch]
2015-11-02 Updated schematic sheets to use the new BR frame.
    [BlueESC.sch]
2015-11-02 Added pdf version of schematic for convenience.
2015-11-02 Added link to pdf schematic in the README.
2015-11-05 Minor updates and reference marking for Vscore.
    [BlueESC.brd]
2015-12-08 Removed a ground via that was too close to a solder point.
    [BlueESC.brd]

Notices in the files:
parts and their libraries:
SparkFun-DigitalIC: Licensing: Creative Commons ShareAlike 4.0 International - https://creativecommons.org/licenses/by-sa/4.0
